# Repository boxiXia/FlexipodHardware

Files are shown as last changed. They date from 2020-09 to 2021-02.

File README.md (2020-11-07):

# FlexipodHardware

## 3D rendering and dimension of Flexipod

CAD model for the Flexipod
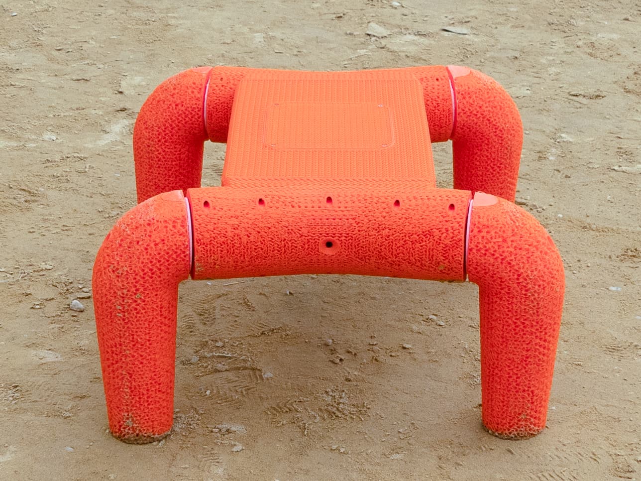
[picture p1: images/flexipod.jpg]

Flexipod stand on sand

## Prerequisite
Software: Inventor and Cura(or some other slice software for 3D printing)     
Filament: [Cheetah flexible filament, Ninjatek](https://ninjatek.com/cheetah/)
          [PolyMax™ PC, Playmaker](https://www.amazon.com/dp/B01KT3K0FW/?coliid=ISKG6U7RH7ZF8&colid=118CNRRRVL2LQ&psc=1&ref_=lv_ov_lig_dp_it)    
Super glue: [Gorilla Super Glue](https://www.amazon.com/Gorilla-Super-Brush-Nozzle-Applicator/dp/B01LYO4R4I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)

## Mechiancl parts

All the printed parts are printed by a FDM 3D printer(Troodon Core-XY printer, VIVEDINO) with a standard 0.4 mm nozzle at 0.2 mm layer height. For soft print, skins are only printed at mating surfaces, since the outer skins of the printed parts will greatly reduce the flexibility.

1. leg: print with 16% infill density(Gyroid pattern) and 80% flow using flexible TPU (Cheetah flexible filament, Ninjatek).
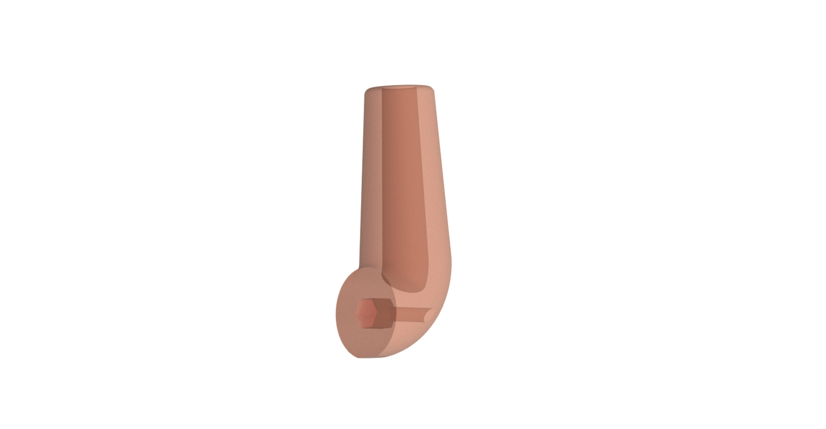
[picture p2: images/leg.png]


2. leg adaptor: rigid filament (PolyMax™ PC, Playmaker)
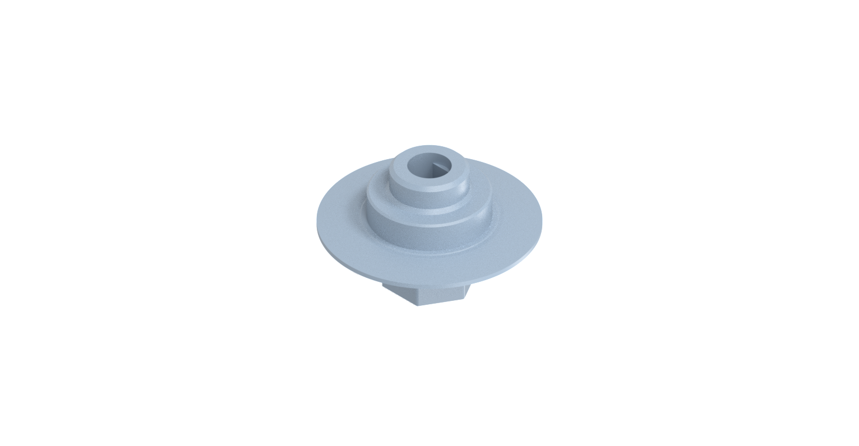
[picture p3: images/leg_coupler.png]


3. motor mount outer part: print with 20% infill density(Gyroid pattern) and 90% flow using flexible TPU (Cheetah flexible filament, Ninjatek).
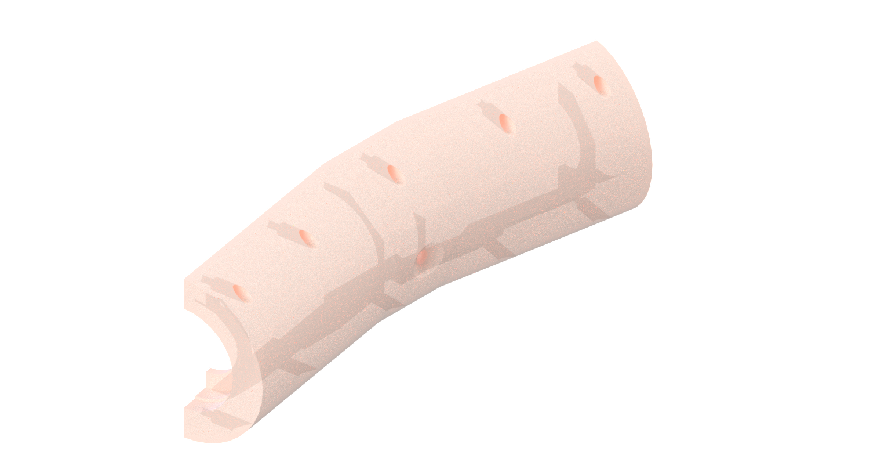
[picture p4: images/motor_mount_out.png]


4. [bearing: ](https://www.amazon.com/6806-Ceramic-Cartridge-Bearing-30x42x7mm/dp/B01MU6Z46A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)
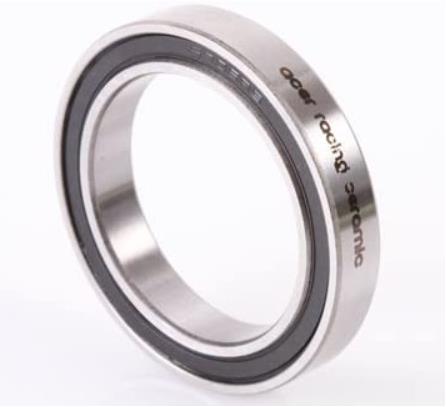
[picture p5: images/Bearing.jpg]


5. motor mount inner part: print with 20% infill density(Gyroid pattern) and 90% flow using flexible TPU (Cheetah flexible filament, Ninjatek).
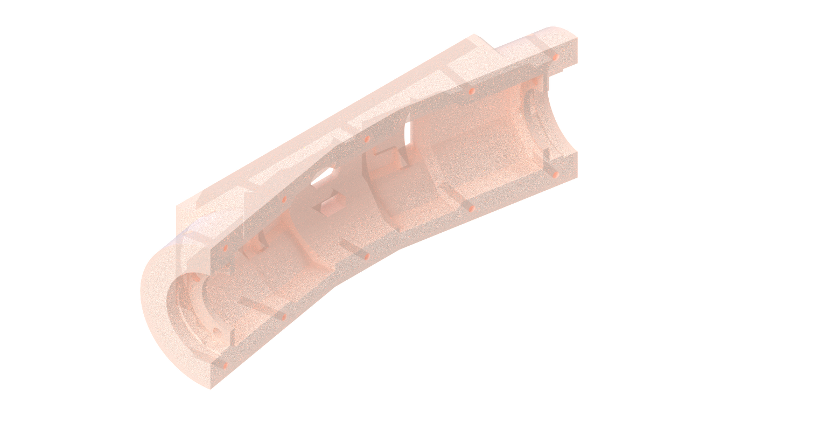
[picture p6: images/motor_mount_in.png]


6. motor shell: rigid filament (PolyMax™ PC, Playmaker)
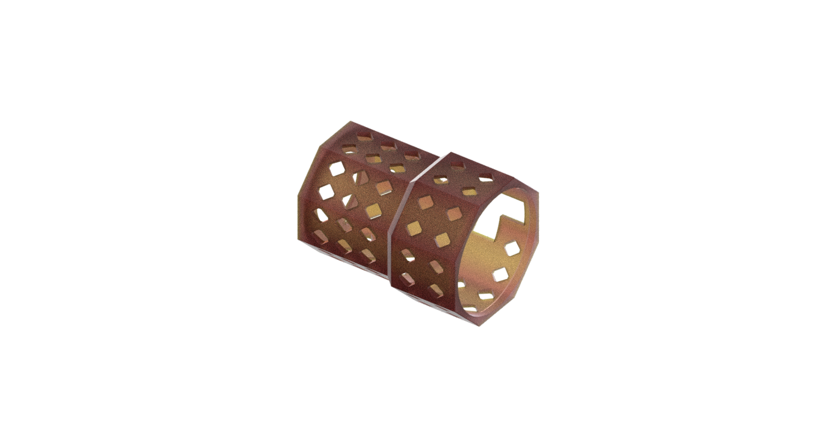
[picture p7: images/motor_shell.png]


7. body cover: print with 20% infill density(Gyroid pattern) and 90% flow using flexible TPU (Cheetah flexible filament, Ninjatek).
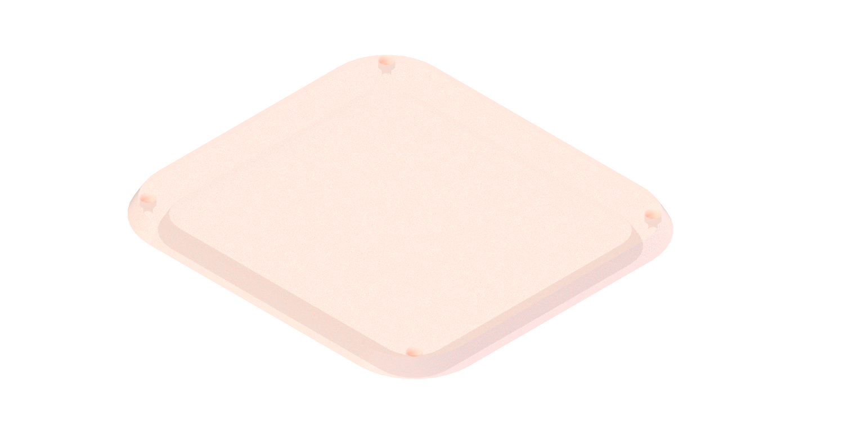
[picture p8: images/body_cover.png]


8. upper body: print with 20% infill density(Gyroid pattern) and 90% flow using flexible TPU (Cheetah flexible filament, Ninjatek).
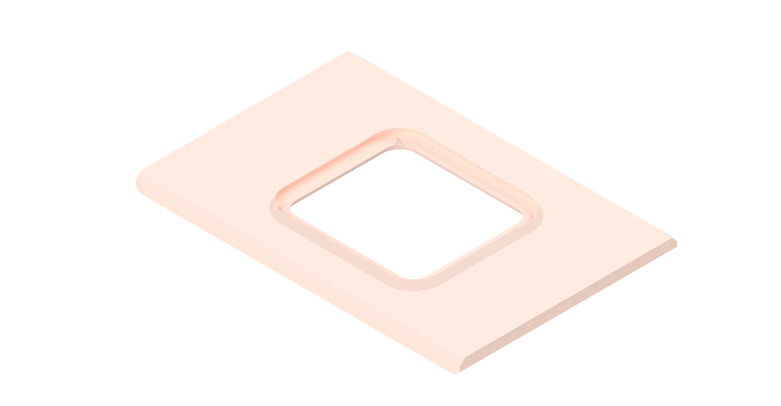
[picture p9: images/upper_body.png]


9. lower body: print with 20% infill density(Gyroid pattern) and 90% flow using flexible TPU (Cheetah flexible filament, Ninjatek).
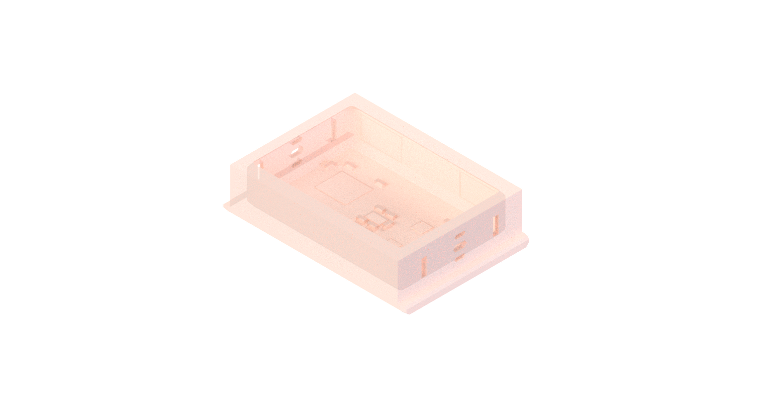
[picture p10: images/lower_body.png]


## Electrical parts
electrical system of the Flexipod  

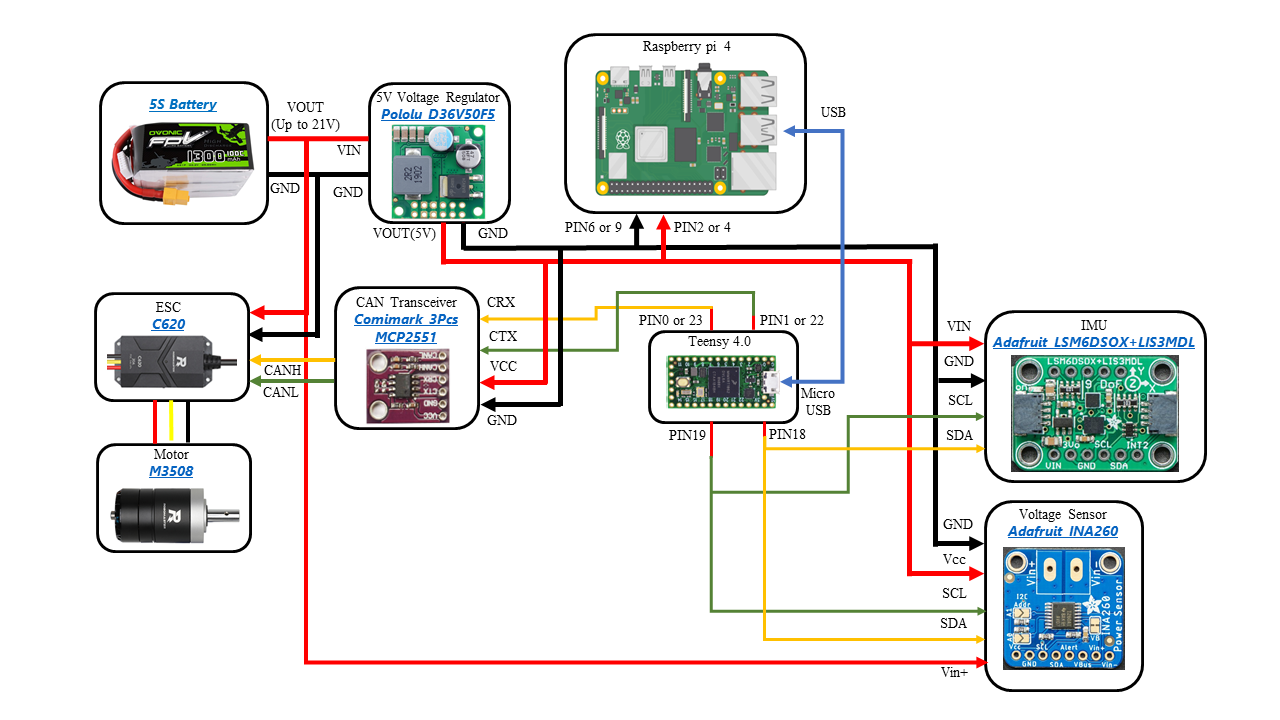
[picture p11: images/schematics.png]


1. [Raspberry Pi 4B](https://www.amazon.com/Raspberry-Model-2019-Quad-Bluetooth/dp/B07TC2BK1X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)

2. [5V Voltage Regulator](https://www.pololu.com/product/4091)

3. [5S Battery](https://www.amazon.com/Ovonic-1300mAh-Battery-Professional-Competitions/dp/B07JXZCHWM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)

4. [CAN Transceivez](https://www.amazon.com/dp/B07V5LGBC8/?coliid=I3FNNXJG3YL6HU&colid=34AXXXH87PSUB&psc=1&ref_=lv_ov_lig_dp_it)

5. [Teensy 4.0](https://www.amazon.com/Teensy-4-0-With-Pins/dp/B08259KDHY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)

6. [IMU](https://www.adafruit.com/product/4517)

7. [Voltage Sensor](https://www.adafruit.com/product/4226)

8. [ESC](https://store.dji.com/product/rm-c620-brushless-dc-motor-speed-controller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)

9. [Motor](https://store.dji.com/product/rm-m3508-p19-brushless-dc-gear-motor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)

10. [Custom PCB](https://github.com/boxiXia/FlexipodHardware/tree/master/mechanical_model/PCB/Gerber%20%26%20drill)

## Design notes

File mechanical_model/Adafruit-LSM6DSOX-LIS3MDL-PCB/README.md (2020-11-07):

## Adafruit LSM6DSOX + LIS3MDL Precision 9-DoF IMU PCBs

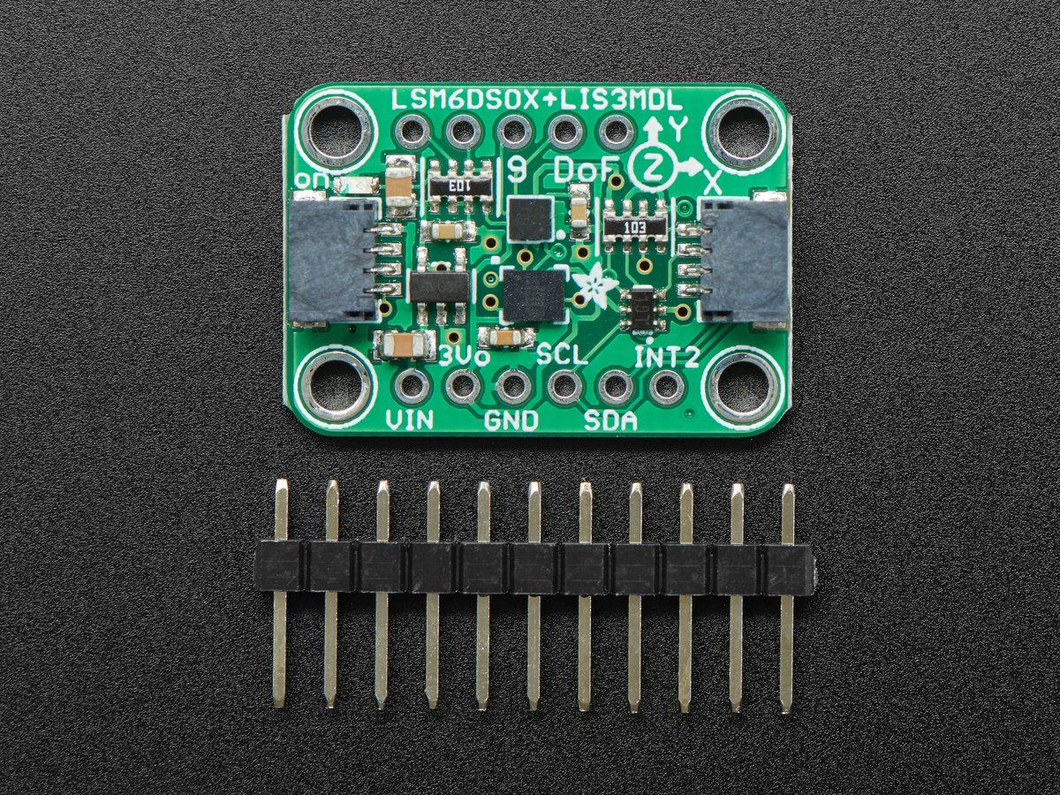
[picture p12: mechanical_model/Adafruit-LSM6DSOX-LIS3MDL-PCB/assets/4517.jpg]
<a href="http://www.adafruit.com/products/4517"><br/>
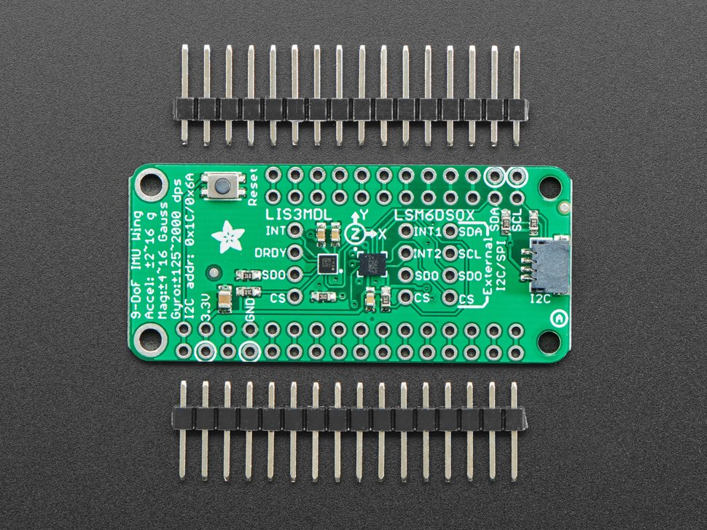
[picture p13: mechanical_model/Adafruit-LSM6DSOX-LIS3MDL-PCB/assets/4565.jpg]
<a href="http://www.adafruit.com/products/4565"><br/>
Click here to purchase one from the Adafruit shop</a>

PCB files for the Adafruit LSM6DSOX + LIS3MDL Precision 9-DoF IMU breakout and FeatherWing.

Format is EagleCAD schematic and board layout
* https://www.adafruit.com/product/4517

### Description

Add high quality motion, direction and orientation sensing to your Arduino project with this all-in-one 9 Degree of Freedom (9-DoF) sensor with sensors from ST. This little breakout contains two chips that sit side-by-side to provide 9 degrees of full-motion data.

The board includes an LSM6DSOX, a 6-DoF IMU accelerometer + gyro. The 3-axis accelerometer can tell you which direction is down towards the Earth (by measuring gravity) or how fast the board is accelerating in 3D space. The 3-axis gyroscope can measure spin and twist. This new sensor from ST has very low gyro zero rate and noise, compared to the MPU6050 or even LSM6DS33 so it's excellent for orientation fusion usage: you'll get less drift and faster responses.

The LSM6DSOX has flexible data rates and ranges. For the accelerometer: ±2/±4/±8/±16 g at 1.6 Hz to 6.7KHz update rate. For the gyroscope: ±125/±250/±500/±1000/±2000 dps at 12.5 Hz to 6.7 KHz. There's also some nice extras, such as built in tap detection, activity detection, pedometer/step counter and a programmable finite state machine / machine learning core that can perform some basic gesture recognition.

It also includes a LIS3MDL 3-axis magnetometer that can sense where the strongest magnetic force is coming from, generally used to detect magnetic north. The three triple-axis sensors add up to 9 degrees of freedom, by combining this data you can orient the board. Check out our guide on how to do that!

To make getting started fast and easy, we placed the sensors on a compact breakout board with voltage regulation and level-shifted inputs. That way you can use them with 3V or 5V power/logic devices without worry. To make usage simple, we expose only the I2C interface and some interrupt pins from each chip. The breakout comes fully assembled and tested, with some extra header so you can use it on a breadboard. Four mounting holes make for a secure connection.

Additionally, since it speaks I2C you can easily connect it up with two wires (plus power and ground!).  We've even included SparkFun qwiic compatible STEMMA QT connectors for the I2C bus so you don't even need to solder! Just wire up to your favorite micro like the STM32F405 Feather with a plug-and-play cable to get 9 DoF data ASAP. You can change the I2C addresses on the back using the solder jumpers, to have two of these sensor boards on one bus.

We also wrote libraries to help you get these sensors integrated with your Arduino/C++. This library covers the accel/gyro and this library is for the magnetometer. For advanced Arduino usage, ST has their own fully-featured library that includes extras such as FIFO management and tap detection for the LSM6DSOX and also for the LIS3MDL magnetometer.

### License

Adafruit invests time and resources providing this open source design, please support Adafruit and open-source hardware by purchasing products from [Adafruit](https://www.adafruit.com)!

Designed by Limor Fried/Ladyada for Adafruit Industries.

Creative Commons Attribution/Share-Alike, all text above must be included in any redistribution.
See license.txt for additional details.

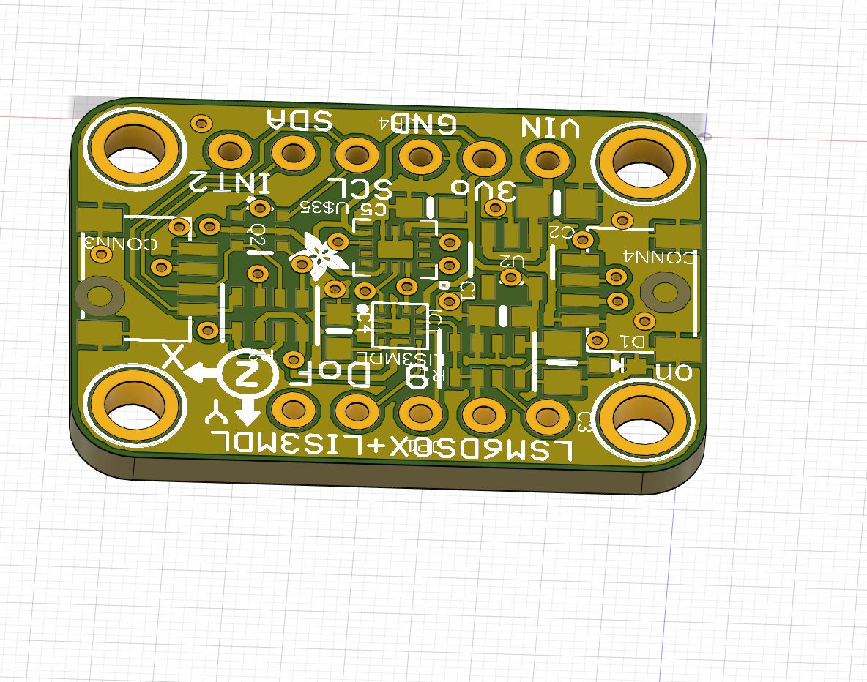
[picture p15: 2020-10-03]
mechanical_model/PCB/Adafruit-LSM6DSOX-LIS3MDL-PCB/Adafruit LIS3MDL + LSM6DSOX (3D).JPG

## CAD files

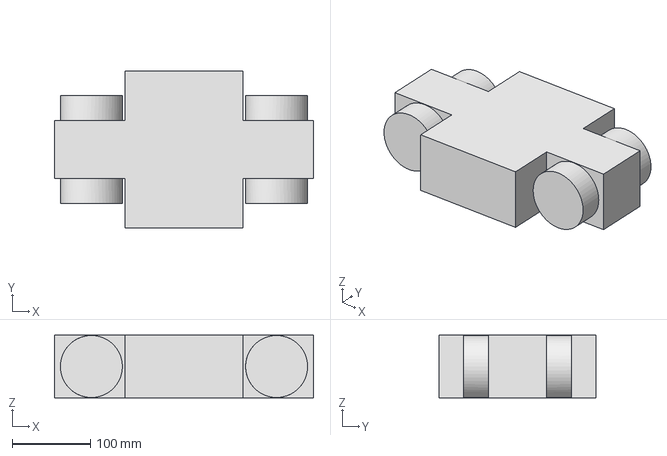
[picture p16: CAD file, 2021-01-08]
Flexipod2.0/Cadquery_module/body.step
330.0 x 200.0 x 80.0 mm

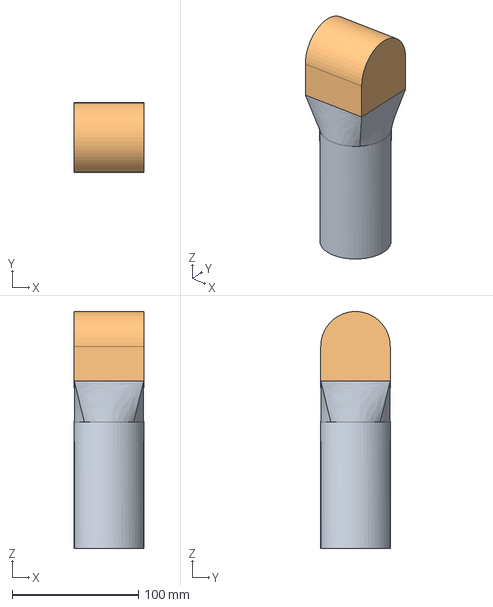
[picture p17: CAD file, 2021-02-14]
Flexipod2.0/Cadquery_module/v8.0/shank.step
55.0 x 55.0 x 187.5 mm

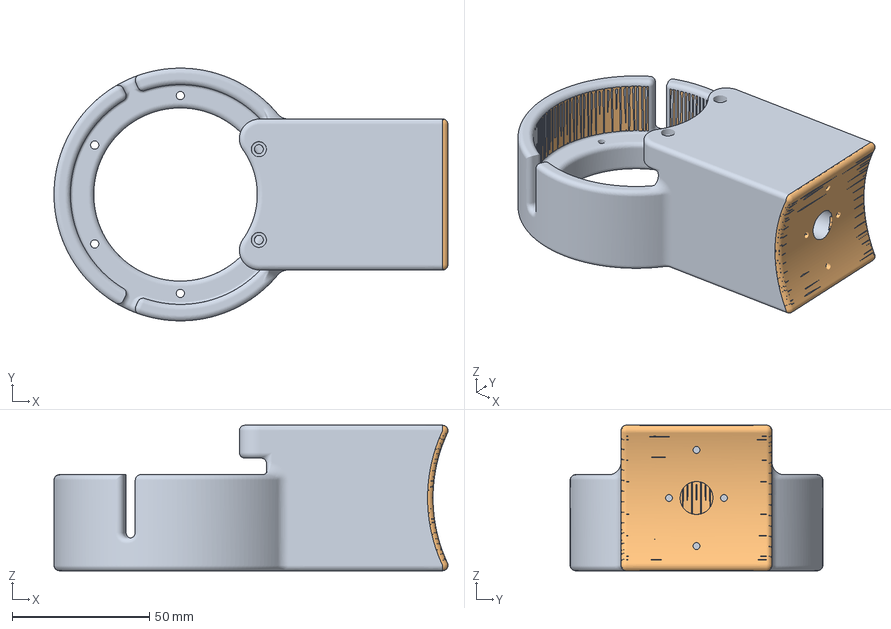
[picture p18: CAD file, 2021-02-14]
Flexipod2.0/print_part/thigh_16infill_80flow.3mf
143.4 x 92.0 x 53.0 mm
thigh_link.ipt
thigh_link.ipt(1)

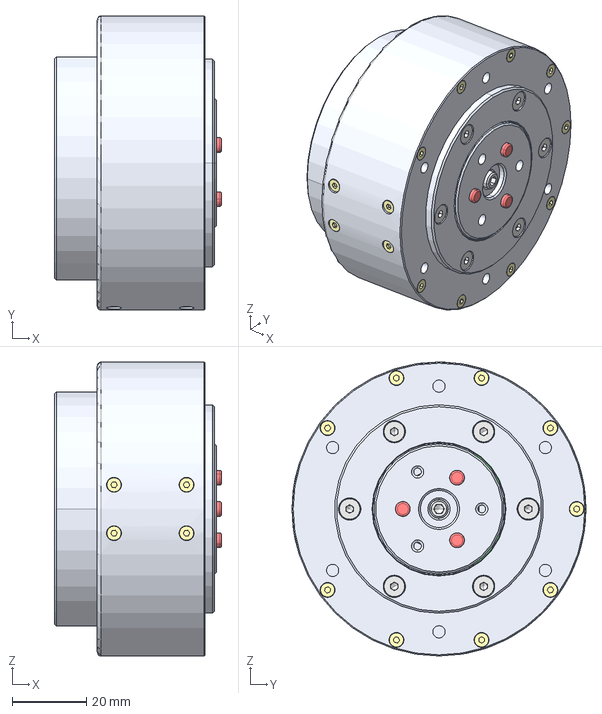
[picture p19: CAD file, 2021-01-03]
Flexipod2.0/RMD_X6.stp
44.9 x 79.0 x 79.0 mm

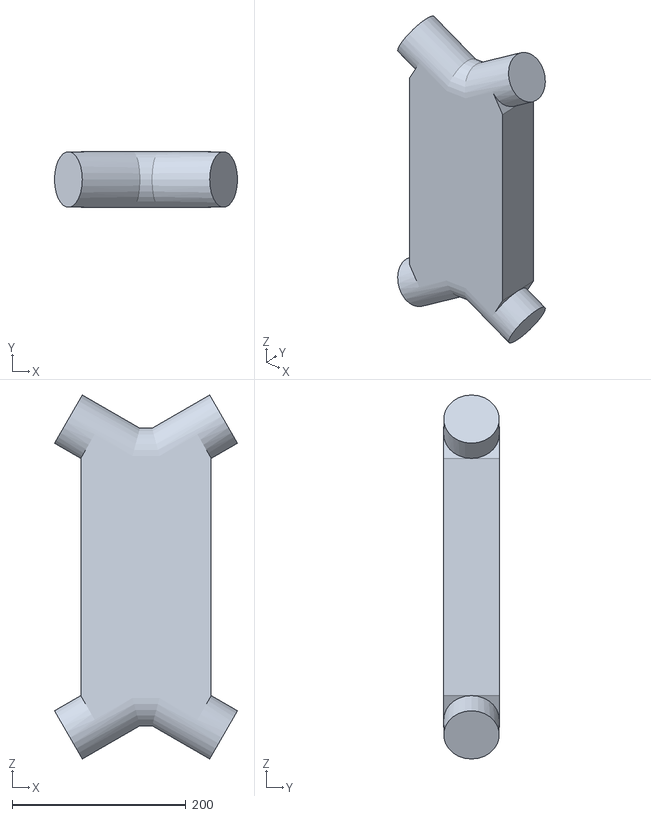
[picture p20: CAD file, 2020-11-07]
mechanical_model/angle_test/soft_body_simplified_30_deg.obj
210.4 x 64.0 x 418.4

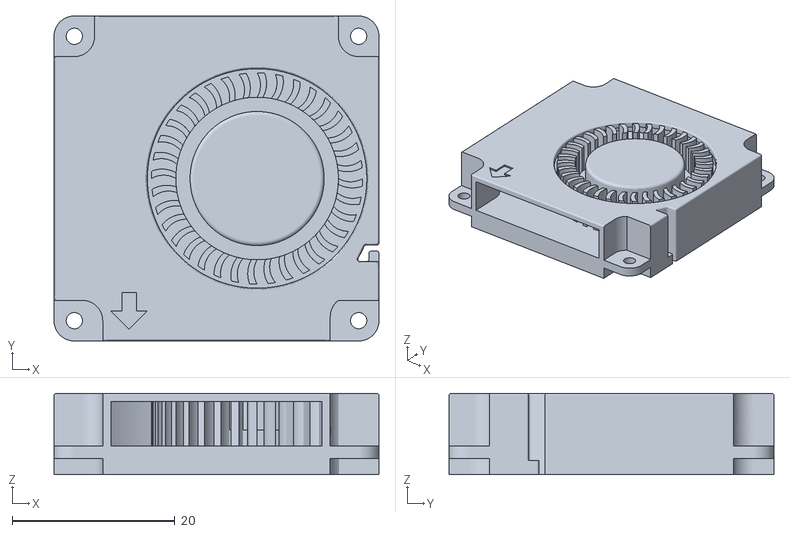
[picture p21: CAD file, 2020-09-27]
mechanical_model/direct_dirve_print_head/4010_Blower_Fan_v2.stl
40.0 x 40.0 x 10.0

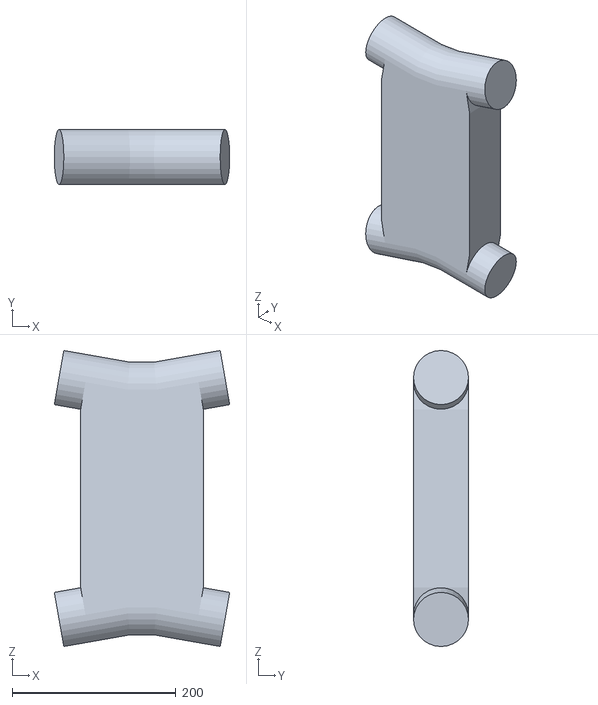
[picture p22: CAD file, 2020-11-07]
mechanical_model/exported_mesh/soft_body_simplified.obj
214.5 x 67.2 x 362.0

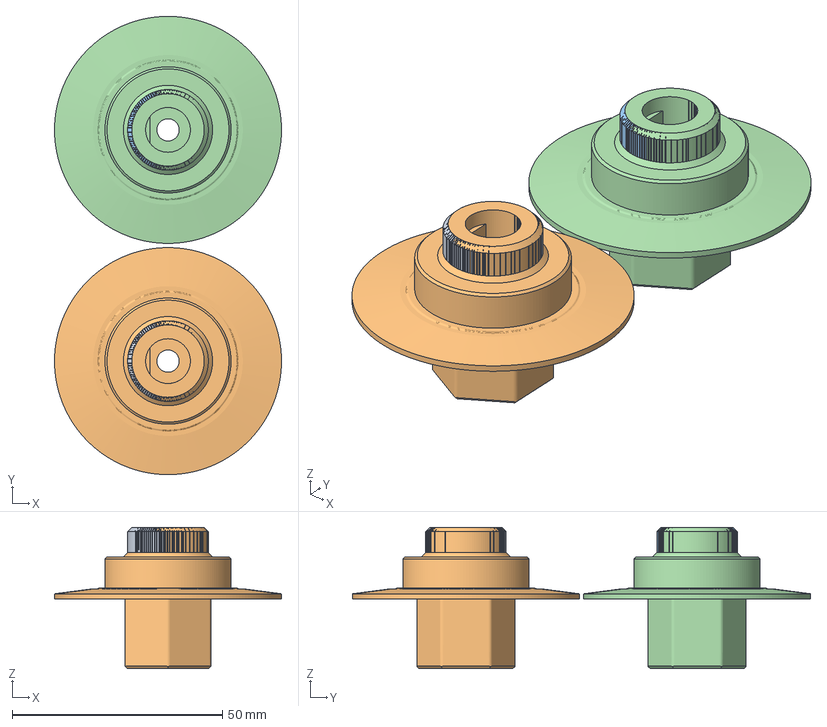
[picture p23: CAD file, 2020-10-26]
mechanical_model/printed_parts/T4_leg_coupler.3mf
54.0 x 109.0 x 33.6 mm
leg_coupler.ipt
leg_coupler.ipt(1)
leg_coupler.ipt(2)
leg_coupler.ipt(3)

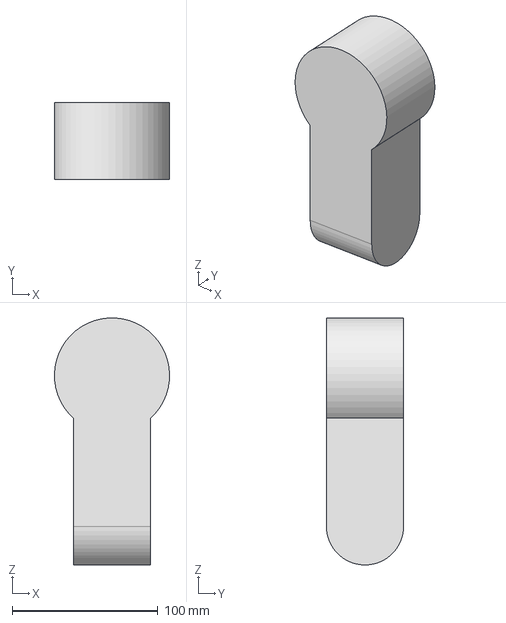
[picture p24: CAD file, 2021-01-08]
Flexipod2.0/Cadquery_module/thigh.step
79.0 x 53.0 x 169.4 mm

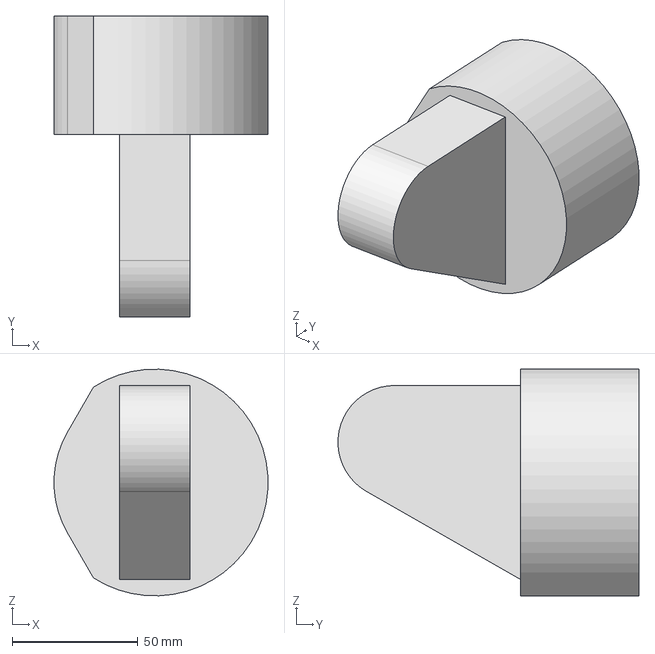
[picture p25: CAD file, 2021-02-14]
Flexipod2.0/Cadquery_module/v8.0/hip_back_mirror.step
84.8 x 119.5 x 89.9 mm

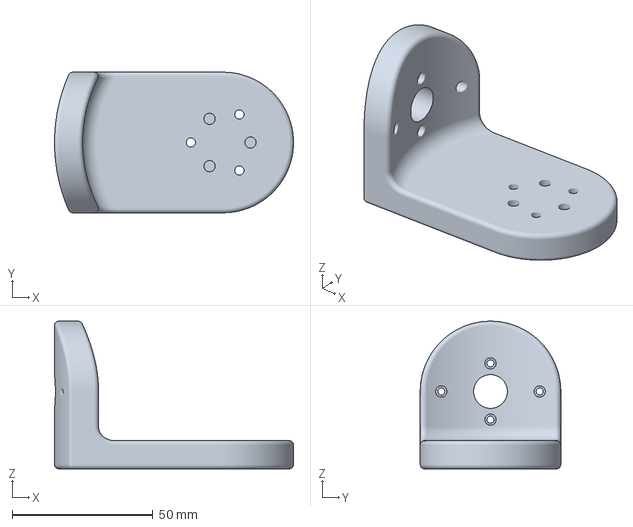
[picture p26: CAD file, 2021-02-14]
Flexipod2.0/print_part/shank_thigh_connector.3mf
85.0 x 50.0 x 52.5 mm

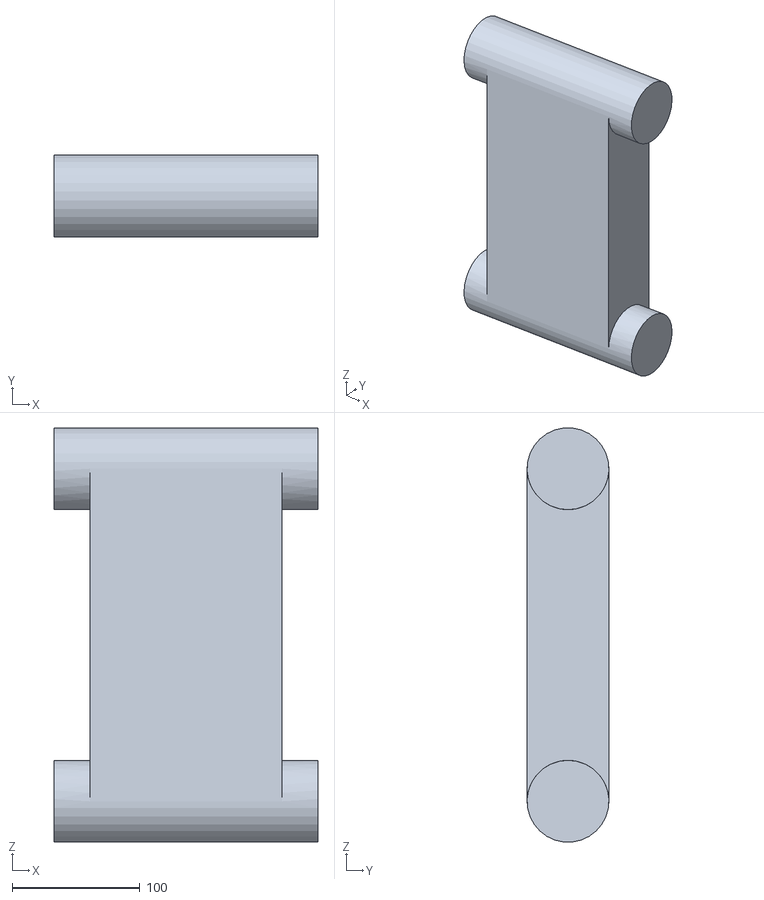
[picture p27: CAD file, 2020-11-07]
mechanical_model/angle_test/soft_body_simplified_00_deg.obj
206.0 x 64.0 x 323.6

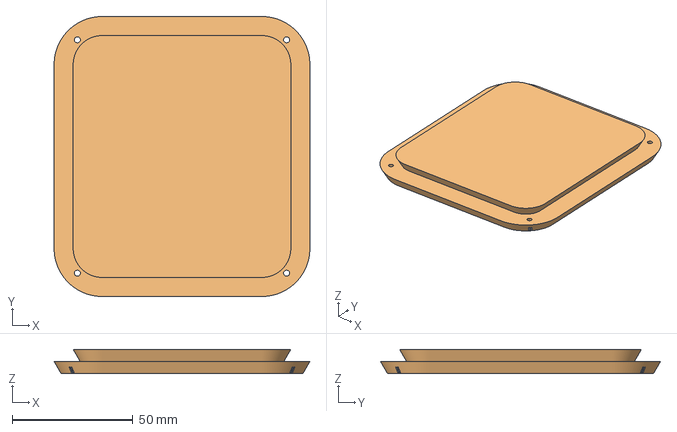
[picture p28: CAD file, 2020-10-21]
mechanical_model/printed_parts/T4_soft_body_motor_cover.3mf
105.8 x 115.8 x 10.0 mm
soft_body.ipt
soft_body.ipt(1)

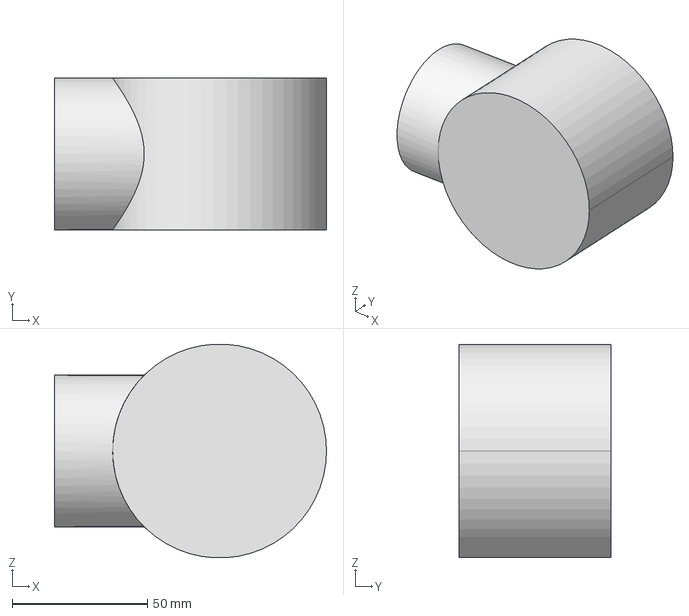
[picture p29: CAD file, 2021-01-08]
Flexipod2.0/Cadquery_module/hip.step
100.5 x 56.0 x 78.9 mm

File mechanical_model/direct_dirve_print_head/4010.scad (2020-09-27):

$fn=1000;
module case() {
    linear_extrude(height = 10, center = true, convexity = 10)
        import (file = "4010.dxf", layer = "0");
}

module corners() {
    linear_extrude(height = 9, center = true, convexity = 10)
        import (file = "4010.dxf", layer = "corners");
}

module fanholle() {
    linear_extrude(height = 9, center = true, convexity = 10)
        import (file = "4010.dxf", layer = "fanholle");
}

module inside() {
    linear_extrude(height = 8, center = true, convexity = 10)
        import (file = "4010.dxf", layer = "inside");
}

module fanself() {
    linear_extrude(height = 9, center = true, convexity = 10)
        import (file = "4010.dxf", layer = "fanself");
}

difference() {
     case();
     translate(v=[0,0,1])
        corners();
     translate(v=[0,0,1])
        fanholle();
    
     inside();
}

fanself();

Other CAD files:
Flexipod2.0/Cadquery_module/v8.0/thigh.step
Flexipod2.0/print_part/front_hip_16infill_80flow.3mf
mechanical_model/angle_test/soft_body_simplified_15_deg.obj
mechanical_model/printed_parts/T4_soft_body_motor_front_out.3mf
Flexipod2.0/Arducam Camera.ipt
Flexipod2.0/Cadquery_module/Simulation_module.iam
Flexipod2.0/Cadquery_module/Simulation_module_2.iam
Flexipod2.0/Cadquery_module/body_inventor.ipt
Flexipod2.0/Cadquery_module/hip_inventor.ipt
Flexipod2.0/Cadquery_module/motor.ipt
Flexipod2.0/Cadquery_module/shank.ipt
Flexipod2.0/Cadquery_module/shank.step
Flexipod2.0/Cadquery_module/v2.0/body.step
Flexipod2.0/Cadquery_module/v2.0/hip_back.step
Flexipod2.0/Cadquery_module/v2.0/hip_front.step
Flexipod2.0/Cadquery_module/v2.0/shank.step
Flexipod2.0/Cadquery_module/v2.0/thigh.step
Flexipod2.0/Cadquery_module/v3.0/body.ipt
Flexipod2.0/Cadquery_module/v3.0/body.step
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

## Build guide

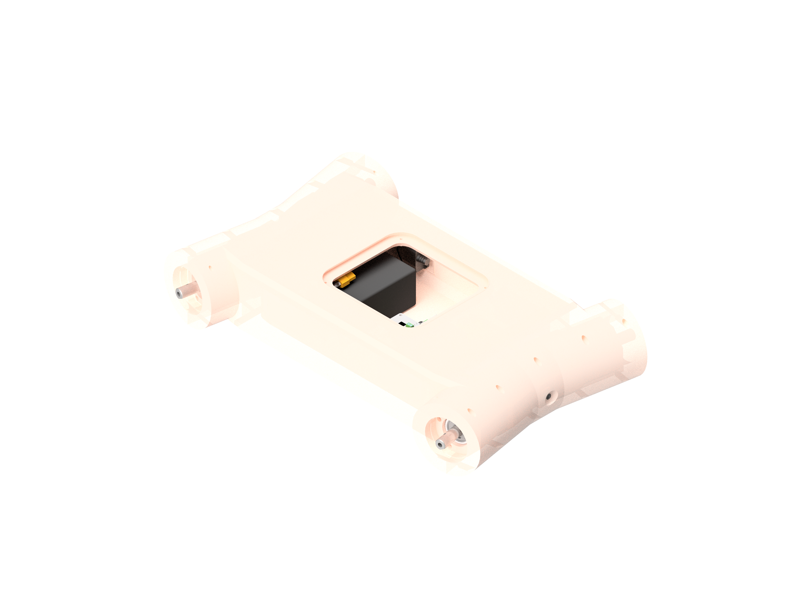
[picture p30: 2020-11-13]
images/flexipod_assembly4.png

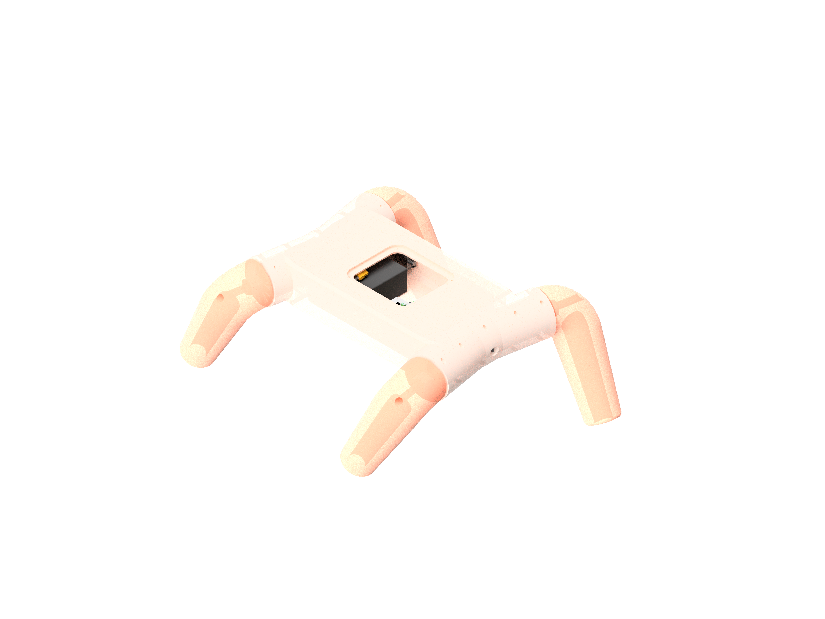
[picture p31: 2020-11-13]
images/flexipod_assembly5.png

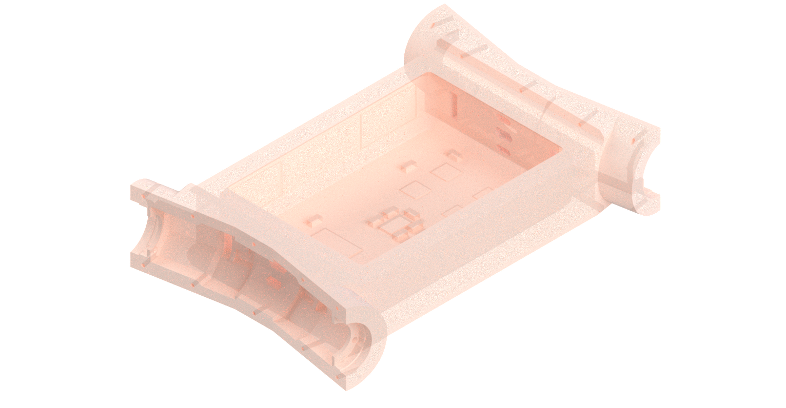
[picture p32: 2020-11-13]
images/flexipod_assembly1.png

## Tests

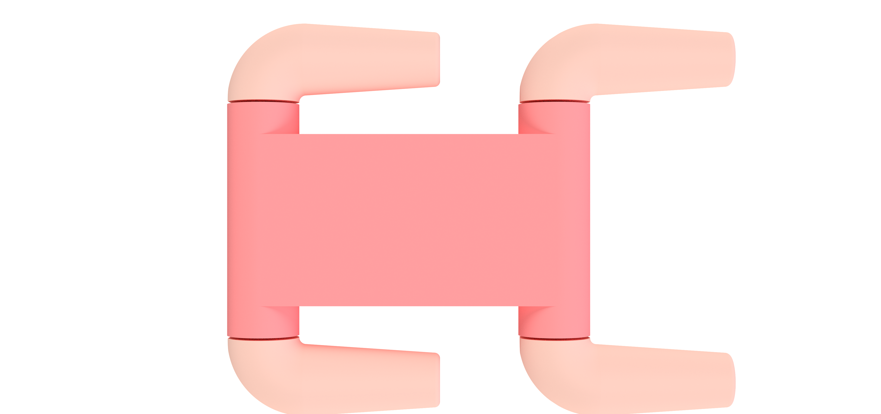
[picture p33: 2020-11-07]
mechanical_model/angle_test/tmp/flexipod_00_deg.png

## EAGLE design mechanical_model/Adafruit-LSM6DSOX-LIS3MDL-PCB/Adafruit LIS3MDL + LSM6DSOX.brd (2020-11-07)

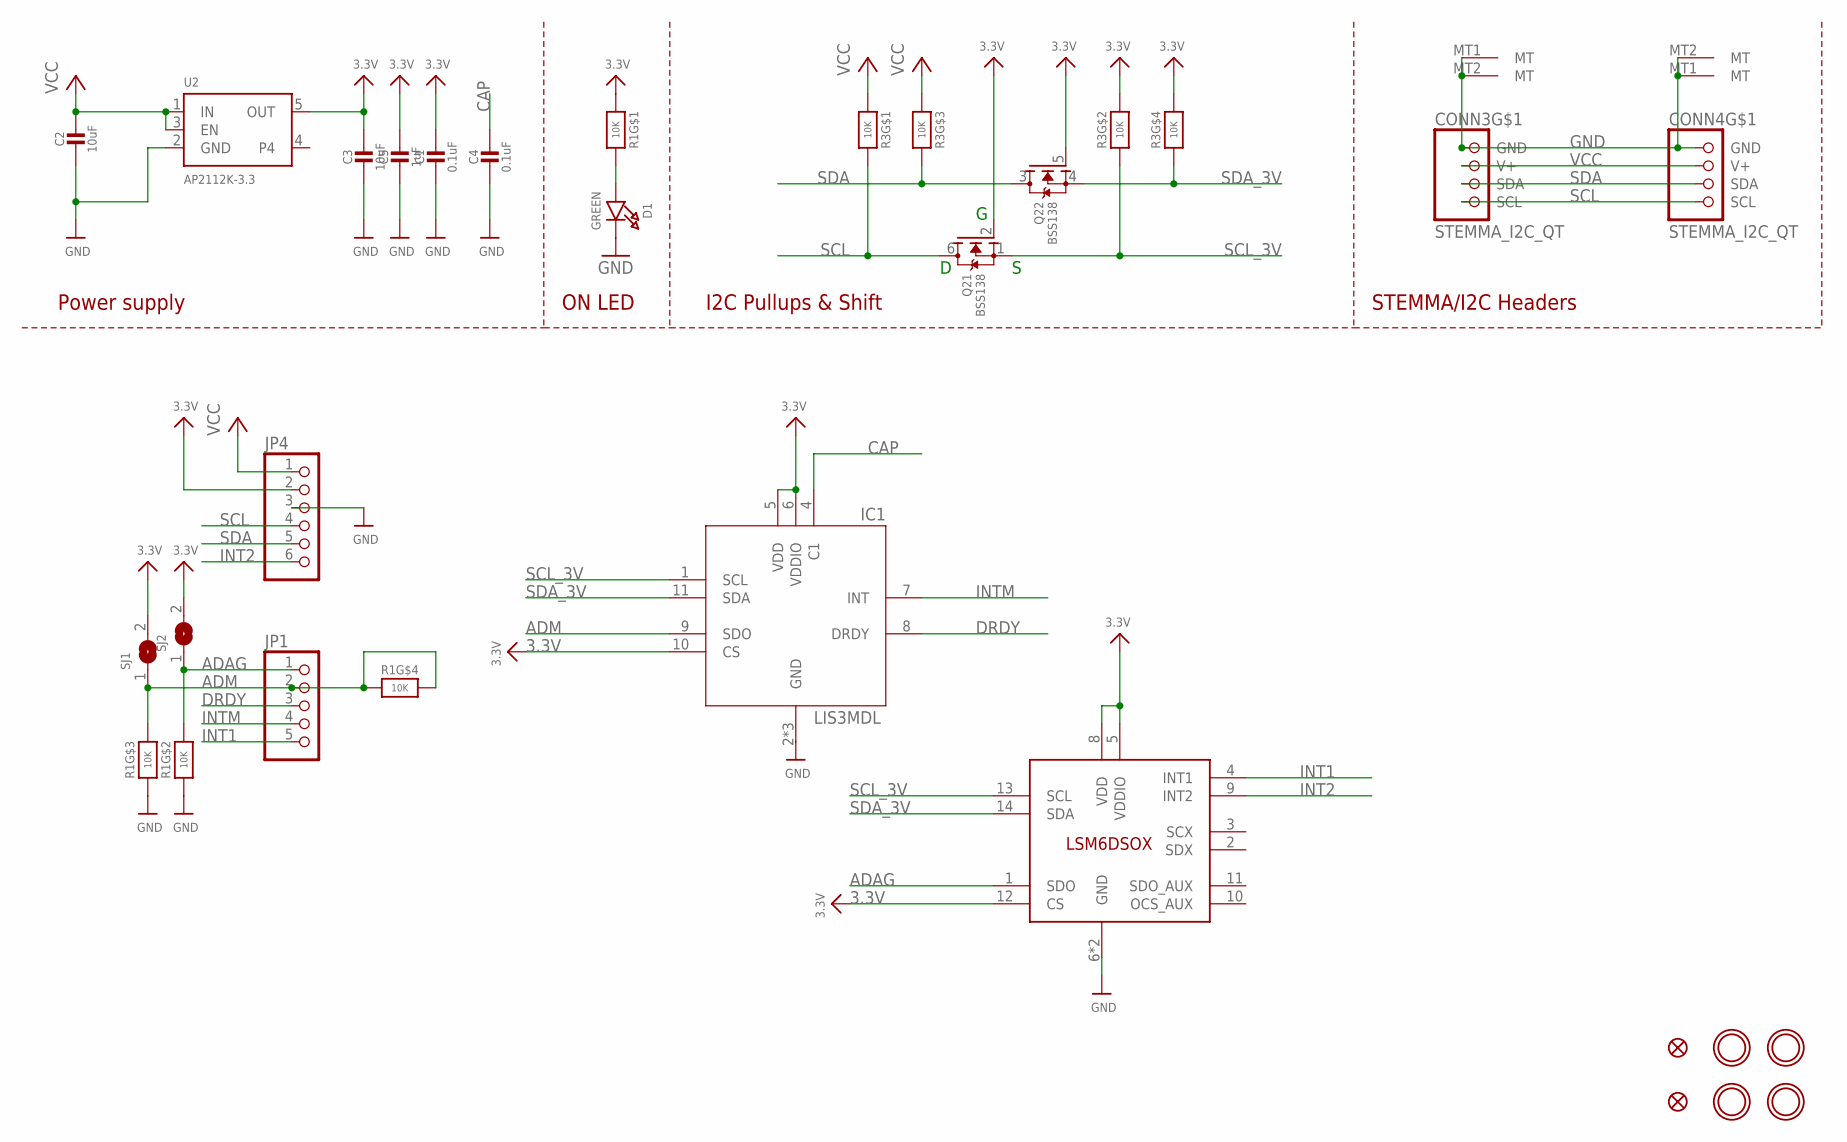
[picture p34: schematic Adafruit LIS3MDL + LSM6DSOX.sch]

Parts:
C1, C4: 0.1uF; 0603-NO
C2, C3: 10uF; 0805-NO
C5: 1uF; 0603-NO
CONN3, CONN4: STEMMA_I2C_QT; JST_SH4
D1: GREEN; CHIPLED_0603_NOOUTLINE
FID3, FID4: FIDUCIAL_1MM
IC1: LIS3MDL; LGA12_2X2MM
JP1: HEADER-1X570MIL; 1X05_ROUND_70
JP4: HEADER-1X670MIL; 1X06_ROUND_70
Q2: BSS138; SOT363
R1, R3: 10K; RESPACK_4X0603
SJ1, SJ2: SOLDERJUMPER; SOLDERJUMPER_ARROW_NOPASTE
U2: AP2112K-3.3; SOT23-5
U$1, U$17, U$19, U$21: MOUNTINGHOLE2.5; MOUNTINGHOLE_2.5_PLATED
U$35: LSM6DSOX; LGA-14L

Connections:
3.3V: C1.1, C3.1, C5.1, IC1.5 (VDD), IC1.6 (VDDIO), IC1.10 (CS), JP4.2, Q2.2 (G), Q2.5 (G), R1.1, R3.2 (1), R3.4 (1), SJ1.2, SJ2.2, U2.5 (OUT), U$35.5 (VDDIO), U$35.8 (VDD), U$35.12 (CS)
ADAG: JP1.1, R1.7 (2), SJ2.1, U$35.1 (SDO)
ADM: IC1.9 (SDO), JP1.2, R1.4 (1), R1.5 (2), R1.6 (2), SJ1.1
CAP: C4.1, IC1.4 (C1)
DRDY: IC1.8 (DRDY), JP1.3
GND: C1.2, C2.2, C3.2, C4.2, C5.2, CONN3.1 (GND), CONN3.MT1 (MT), CONN3.MT2 (MT), CONN4.1 (GND), CONN4.MT1 (MT), CONN4.MT2 (MT), D1.C, IC1.2 (GND), IC1.3 (GND), IC1.12 (GND), JP4.3, R1.2 (1), R1.3 (1), U2.2 (GND), U$35.6 (GND), U$35.7 (GND)
INT1: JP1.5, U$35.4 (INT1)
INT2: JP4.6, U$35.9 (INT2)
INTM: IC1.7 (INT), JP1.4
unnamed: D1.A, R1.8 (2)
SCL: CONN3.4 (SCL), CONN4.4 (SCL), JP4.4, Q2.6 (D), R3.8 (2)
SCL_3V: IC1.1 (SCL), Q2.1 (S), R3.7 (2), U$35.13 (SCL)
SDA: CONN3.3 (SDA), CONN4.3 (SDA), JP4.5, Q2.3 (D), R3.6 (2)
SDA_3V: IC1.11 (SDA), Q2.4 (S), R3.5 (2), U$35.14 (SDA)
VCC: C2.1, CONN3.2 (V+), CONN4.2 (V+), JP4.1, R3.1, R3.3 (1), U2.1 (IN), U2.3 (EN)

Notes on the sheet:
I2C Pullups & Shift
STEMMA/I2C Headers
ON LED
Power supply

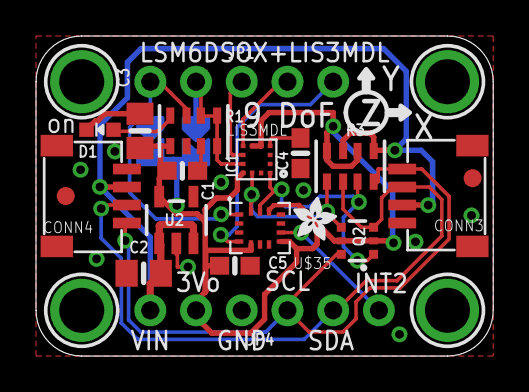
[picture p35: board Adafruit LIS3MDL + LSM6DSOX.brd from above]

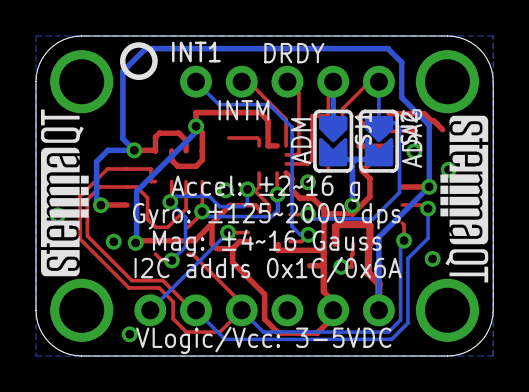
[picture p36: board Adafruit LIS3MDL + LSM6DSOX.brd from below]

Board: 2 copper layers, 25.4 x 17.8 mm, 28 parts (5 on the bottom side), 15 nets.

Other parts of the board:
U$20: ADAFRUIT_2.5MM
U$25: PCBFEAT-REV-040
U$30, U$31: STEMMAQT

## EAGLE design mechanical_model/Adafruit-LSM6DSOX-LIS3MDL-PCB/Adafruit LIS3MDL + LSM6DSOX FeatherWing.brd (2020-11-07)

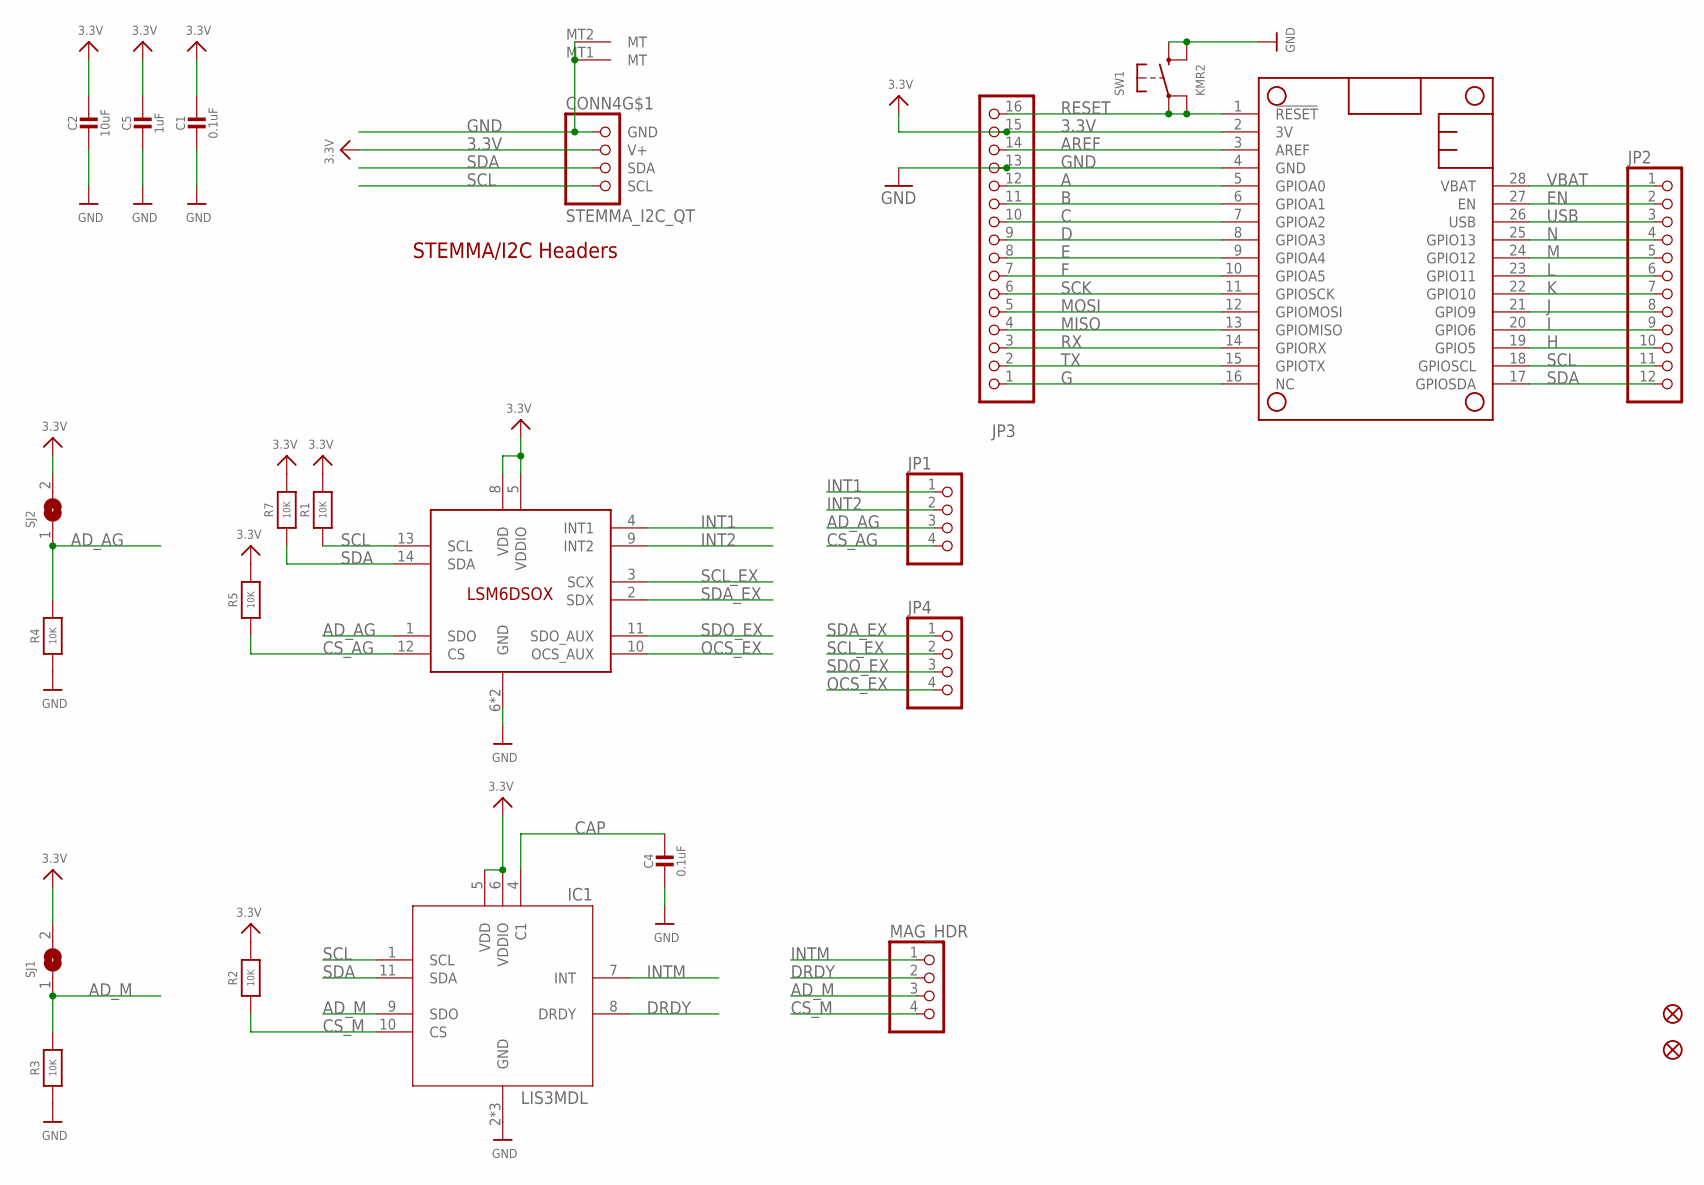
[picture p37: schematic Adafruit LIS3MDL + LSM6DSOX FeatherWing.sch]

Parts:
C1, C4: 0.1uF; 0603-NO
C2: 10uF; 0805-NO
C5: 1uF; 0603-NO
CONN4: STEMMA_I2C_QT; JST_SH4
FID1, FID2: FIDUCIAL_1MM
IC1: LIS3MDL; LGA12_2X2MM
JP1, JP4: HEADER-1X4ROUND; 1X04_ROUND
JP2: HEADER-1X12; 1X12_ROUND
JP3: HEADER-1X16ROUND; 1X16_ROUND
MAG_HDR: HEADER-1X4ROUND; 1X04_ROUND
MS1: FEATHERWING
R1, R2, R3, R4, R5, R7: 10K; 0603-NO
SJ1, SJ2: SOLDERJUMPER; SOLDERJUMPER_ARROW_NOPASTE
SW1: KMR2; BTN_KMR2_4.6X2.8
U$35: LSM6DSOX; LGA-14L

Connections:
3.3V: C1.1, C2.1, C5.1, CONN4.2 (V+), IC1.5 (VDD), IC1.6 (VDDIO), JP3.15, MS1.2 (3V), R1.2, R2.2, R5.2, R7.2, SJ1.2, SJ2.2, U$35.5 (VDDIO), U$35.8 (VDD)
A: JP3.12, MS1.5 (GPIOA0)
AD_AG: JP1.3, R4.2, SJ2.1, U$35.1 (SDO)
AD_M: IC1.9 (SDO), MAG_HDR.3, R3.2, SJ1.1
AREF: JP3.14, MS1.3 (AREF)
B: JP3.11, MS1.6 (GPIOA1)
C: JP3.10, MS1.7 (GPIOA2)
CAP: C4.1, IC1.4 (C1)
CS_AG: JP1.4, R5.1, U$35.12 (CS)
CS_M: IC1.10 (CS), MAG_HDR.4, R2.1
D: JP3.9, MS1.8 (GPIOA3)
DRDY: IC1.8 (DRDY), MAG_HDR.2
E: JP3.8, MS1.9 (GPIOA4)
EN: JP2.2, MS1.27 (EN)
F: JP3.7, MS1.10 (GPIOA5)
G: JP3.1, MS1.16 (NC)
GND: C1.2, C2.2, C4.2, C5.2, CONN4.1 (GND), CONN4.MT1 (MT), CONN4.MT2 (MT), IC1.2 (GND), IC1.3 (GND), IC1.12 (GND), JP3.13, MS1.4 (GND), R3.1, R4.1, SW1.B (S), SW1.B' (S1), U$35.6 (GND), U$35.7 (GND)
H: JP2.10, MS1.19 (GPIO5)
I: JP2.9, MS1.20 (GPIO6)
INT1: JP1.1, U$35.4 (INT1)
INT2: JP1.2, U$35.9 (INT2)
INTM: IC1.7 (INT), MAG_HDR.1
J: JP2.8, MS1.21 (GPIO9)
K: JP2.7, MS1.22 (GPIO10)
L: JP2.6, MS1.23 (GPIO11)
M: JP2.5, MS1.24 (GPIO12)
MISO: JP3.4, MS1.13 (GPIOMISO)
MOSI: JP3.5, MS1.12 (GPIOMOSI)
N: JP2.4, MS1.25 (GPIO13)
OCS_EX: JP4.4, U$35.10 (OCS_AUX)
RESET: JP3.16, MS1.1 (!RESET), SW1.A, SW1.A' (P1)
RX: JP3.3, MS1.14 (GPIORX)
SCK: JP3.6, MS1.11 (GPIOSCK)
SCL: CONN4.4 (SCL), IC1.1 (SCL), JP2.11, MS1.18 (GPIOSCL), R1.1, U$35.13 (SCL)
SCL_EX: JP4.2, U$35.3 (SCX)
SDA: CONN4.3 (SDA), IC1.11 (SDA), JP2.12, MS1.17 (GPIOSDA), R7.1, U$35.14 (SDA)
SDA_EX: JP4.1, U$35.2 (SDX)
SDO_EX: JP4.3, U$35.11 (SDO_AUX)
TX: JP3.2, MS1.15 (GPIOTX)
USB: JP2.3, MS1.26 (USB)
VBAT: JP2.1, MS1.28 (VBAT)

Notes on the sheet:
STEMMA/I2C Headers

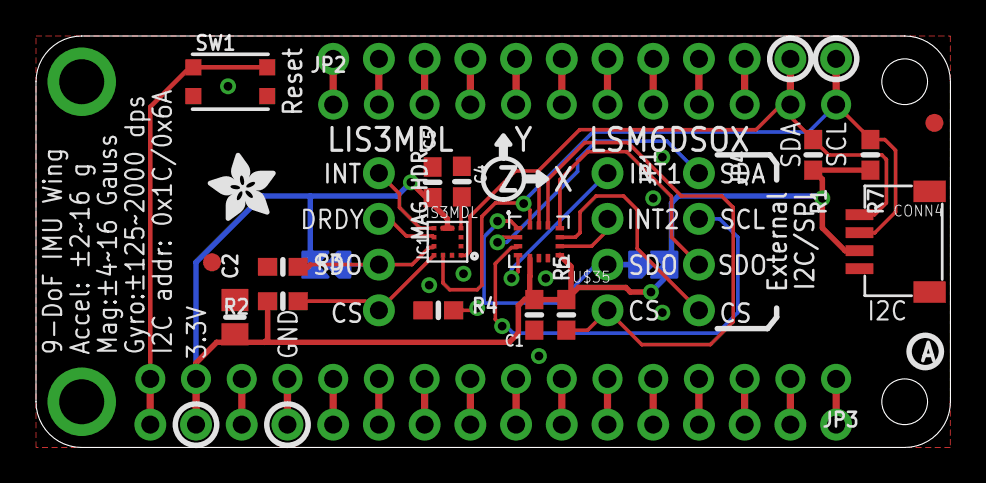
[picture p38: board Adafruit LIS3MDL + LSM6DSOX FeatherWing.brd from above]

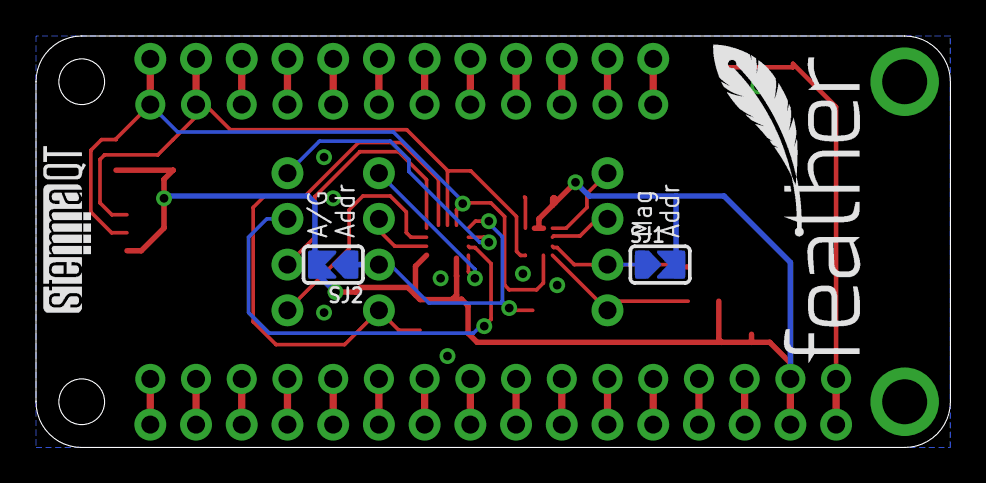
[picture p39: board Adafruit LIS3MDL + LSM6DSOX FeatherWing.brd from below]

Board: 2 copper layers, 50.8 x 22.9 mm, 28 parts (4 on the bottom side), 41 nets.

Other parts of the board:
U$13: FEATHERLOGO_MED
U$31: STEMMAQT
U$50: ADAFRUIT_3.5MM
U$51: PCBFEAT-REV-040

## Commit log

2020-09-30 bigger and longer version with camera
    [26_ASM.0007.iam, 26_ASM.iam, 2_ASM.0007.iam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]
2020-10-03 clean up
    [1-copper.0001.ipt, 1-soldermask.0002.ipt, 1-soldermask.0004.ipt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]
2020-10-03 Main body modified 10/3/2020
    [T4_soft_body_v2.4_motor_front_out.3mf]
2020-10-04 Change skin for mount_front_in & out part
    [T4_soft_body_v2.4_motor_front_in.3mf, T4_soft_body_v2.4_motor_front_out.3mf]
2020-10-05 body modified 10_5_2020
    [T4_soft_body_v2.4_body_down.3mf, leg.ipt]
2020-10-05 Auto stash before merge of "master" and "origin/master"
    [flexipod_assembly_simplified.iam, leg.ipt, soft_body_simplified.ipt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]
2020-10-06 edit model for printing 2020 10 6
    [T4_soft_body_v2.4_body_cover.3mf, T4_soft_body_v2.4_body_down.3mf, T4_soft_body_v2.4_body_up.3mf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]
2020-10-07 changed leg geometry
    [flexipod_assembly_simplified.iam, leg.ipt, soft_body_simplified.ipt]
2020-10-16 add test block
    [T4_leg_4x_16infill_70flow.3mf, T4_shore-A-test-block-cube.3mf, T4_shore-A-test-block-dome.3mf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]
2020-10-16 lesser skin version
    [T4_soft_body_down.3mf]
2020-10-16 update lesser skin version
    [flexipod_assembly_simplified.iam]
2020-10-17 motor front in
    [T4_soft_body_motor_front_in.3mf, T4_soft_body_up.3mf]
2020-10-17 motor front out
    [T4_soft_body_motor_front_out.3mf]
2020-10-21 stronger coupler
    [T4_leg_coupler.3mf, leg_coupler.ipt]
2020-11-07 Gerber and drill file
    [PCB version4.GBL, PCB version4.GBO, PCB version4.GBP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]
2021-01-04 new version of robot
    [body.0005.ipt, body.ipt, body_2020_12_28_13_34.0024.ipt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]
2021-01-05 Cadquery module
    [142-13449-1000-B01-SKU0000.0001.iam, 600-13448_PORG_MODULE_PCB_ASSY.0001.iam, 600-13449_PORG_DEV_KIT_PCB_ASSY.0001.iam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]
2021-01-06 new robot
    [Flexipod2.0_2021_1_6.0002.iam, Flexipod2.0_2021_1_6.iam, Flexipod2.0_2021_1_6_2.0002.iam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]
2021-01-10 new robot body
    [Assembly1.iam, Flexipod2.0_2021_1_6_2.0003.iam, Flexipod2.0_2021_1_6_2.iam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]
2021-01-29 remove oldversion
    [Simulation_module.0015.iam, Simulation_module.0017.iam, Simulation_module.iam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]
2021-01-29 add schematics
    [body.0004.ipt, body.ipt, hip.0002.ipt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]
2021-02-14 2021_2_13 new robot and animation
    [Part5.0005.ipt, back_hip_cable_protector.ipt, back_motor_fix_board.ipt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]

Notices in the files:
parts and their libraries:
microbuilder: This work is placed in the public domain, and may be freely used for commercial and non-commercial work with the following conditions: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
